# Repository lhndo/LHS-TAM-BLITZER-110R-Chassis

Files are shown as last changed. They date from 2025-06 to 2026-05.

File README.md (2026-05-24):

# LHS TAM BLITZER 1/10 R Chassis
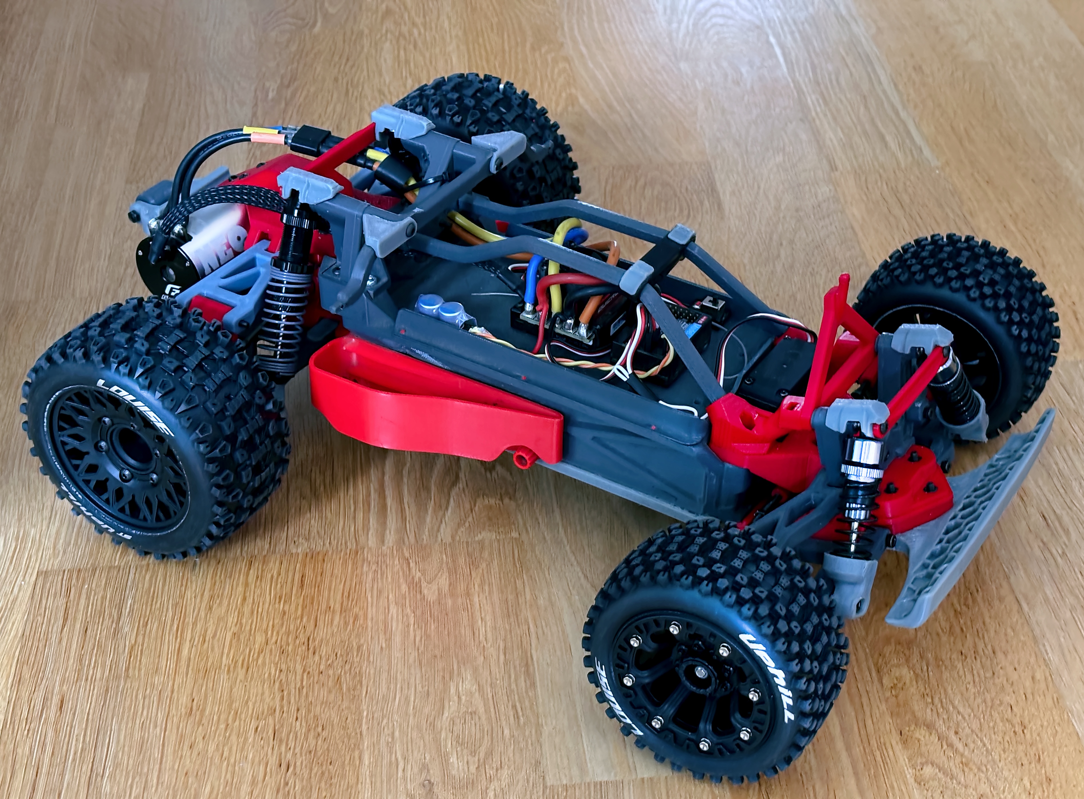
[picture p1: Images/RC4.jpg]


## Video

https://youtu.be/My_7cAeliWg

## Description

This is a FDM redesign exercise based on the 1/10 scale Tamiya Blitzer R/C chassis released in 1992 with the Tamiya Stadium Blitzer car, and later with the Tamiya Blitzer Beetle (my original kit).  

The project started with the intention of stiffening some of the original parts and having a source of spares which I could print, but ended up with a complete redesign that took a month an a half.  
I have tried to match the mounting points, so most of the parts are interchangeable with the original chassis, noting that my references were my trusty calipers and my Tamiya kit.  

The provided body posts are compatible with the Tamiya Blitzer Beetle Hard Shell Body  

### Specs

Motor: G-Force Neo Fast 13.5T Sensored Brushless Motor (2700KV) on a 13T pinion (10:1 final ratio)  
ESC: QUICRUN 10BL120 SENSORED G2  
Battery: Voltz 4600mAh 7.2V NiMh  
Weight: 2250g (4600mAh NiMh battery included)

# CAD
[Online CAD Viewer](http://tiny.cc/lhs-rc1)

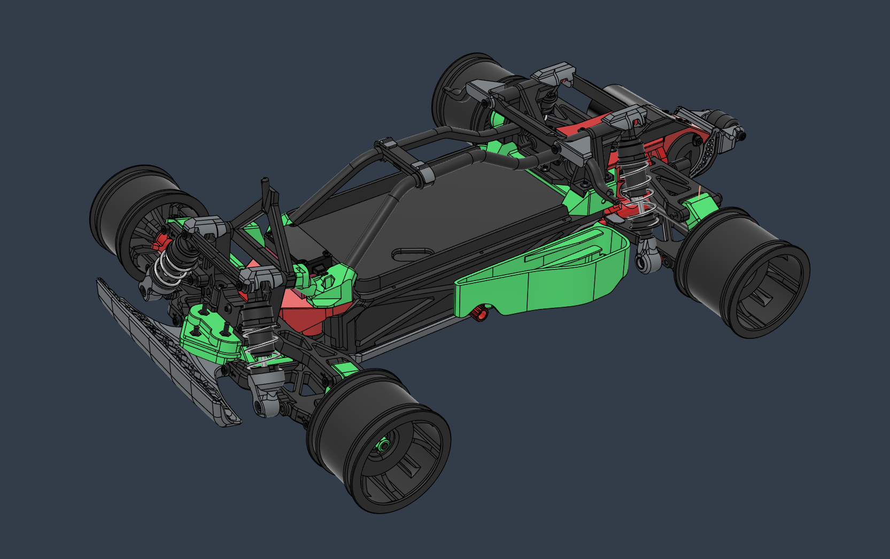
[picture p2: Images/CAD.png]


# Print

- The provided 3mf project files are set up for Orca Slicer and have extensive per-part settings for best print/performance

PLA+
_(Initial prototypes were printed in PCTG/PETG, but PLA+ with high toughness fared much better long term)_

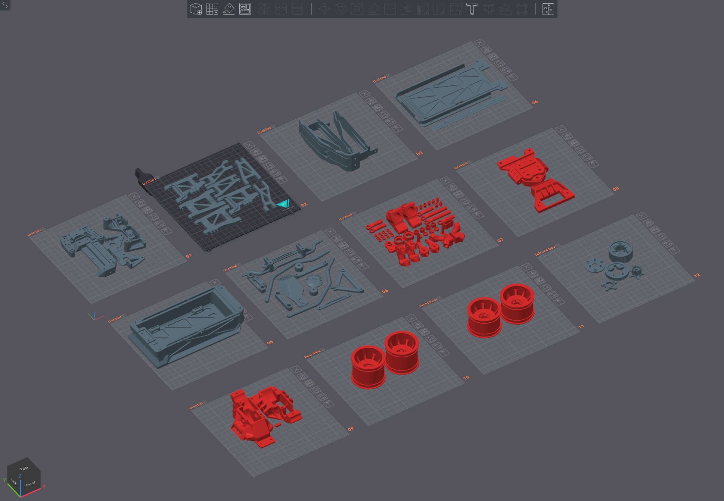
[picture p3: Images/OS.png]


TPU (95/98A)

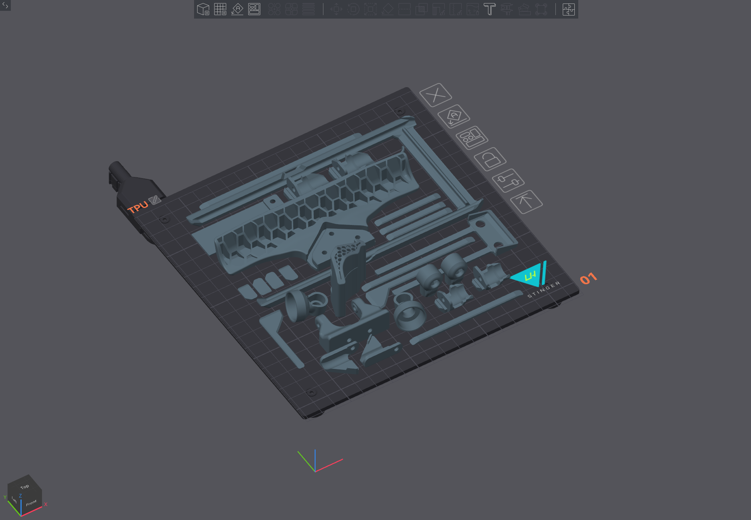
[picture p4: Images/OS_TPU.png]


# BOM

[BOM](https://docs.google.com/spreadsheets/d/1pdifgY0qCpqBBOGrd_-9JSDsqHa0moP6McLiiB6KZIc/edit?usp=sharing)

# Assembly

- Reference [Online CAD Viewer](http://tiny.cc/lhs-rc1)
- Hardware Reference Guide :

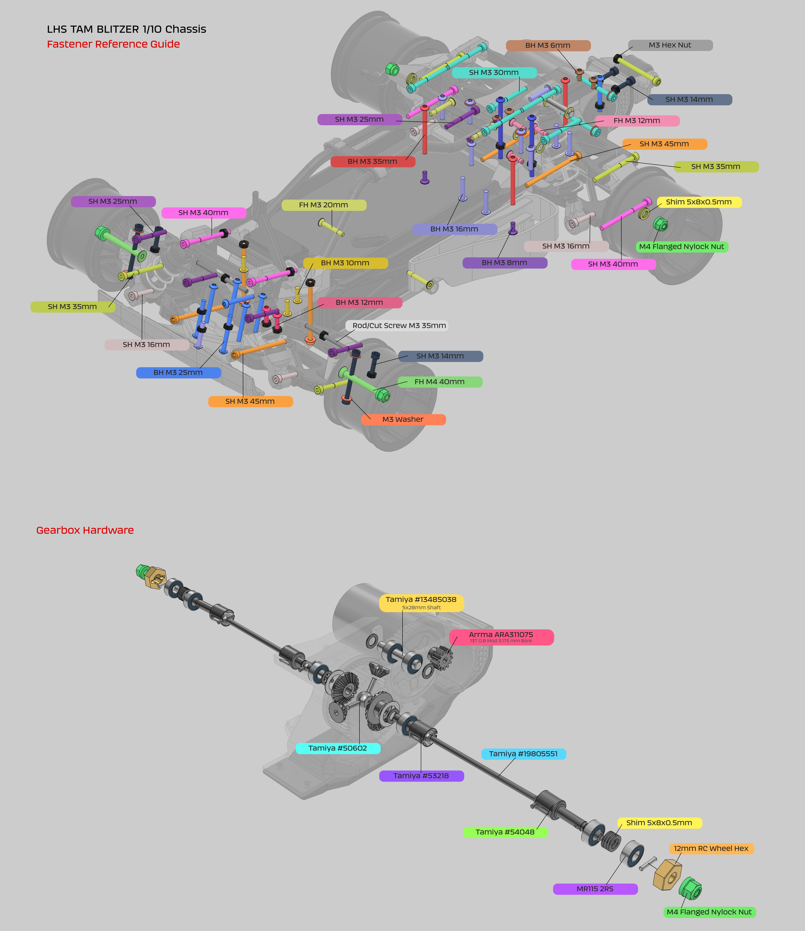
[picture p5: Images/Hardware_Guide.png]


Notes:

- Break away sacrificial bridges and clean up support areas
- The rear suspension post is composed by two parts that need to be glued together. 
  - Use filament dowels for alignment.
  - Do the same for the attachments on the main body/battery box. 
- Use an M3 tap for parts that screw directly into the plastic. These are designed with 2.6mm diameter holes that HAVE to be tapped.
- Don't over torque the screws
- Expect parts to be stiffer in the beginning and loosen up after a break-in period 
- Inject Super Lube into the holes that receive screws as axles (arms, hubs, etc). 
- Add a generous amount of Super Lube to the spur gears, differential (inside and out), and pinion gear.  
- Glue the TPU parts with Loctite Extreme Glue, Shoe Glue, E6000 etc.
- Don't overtighten the M4 lock nuts on the front wheels. Just enough so they spin freely.
- Lock the wheelie bar nut with CA glue
- Lock the middle nut on the steering faux turnbuckle screws with CA glue
- For best performance the tires will need to be set with foams and glued to the rim 
- Enjoy!

<br>

# Media





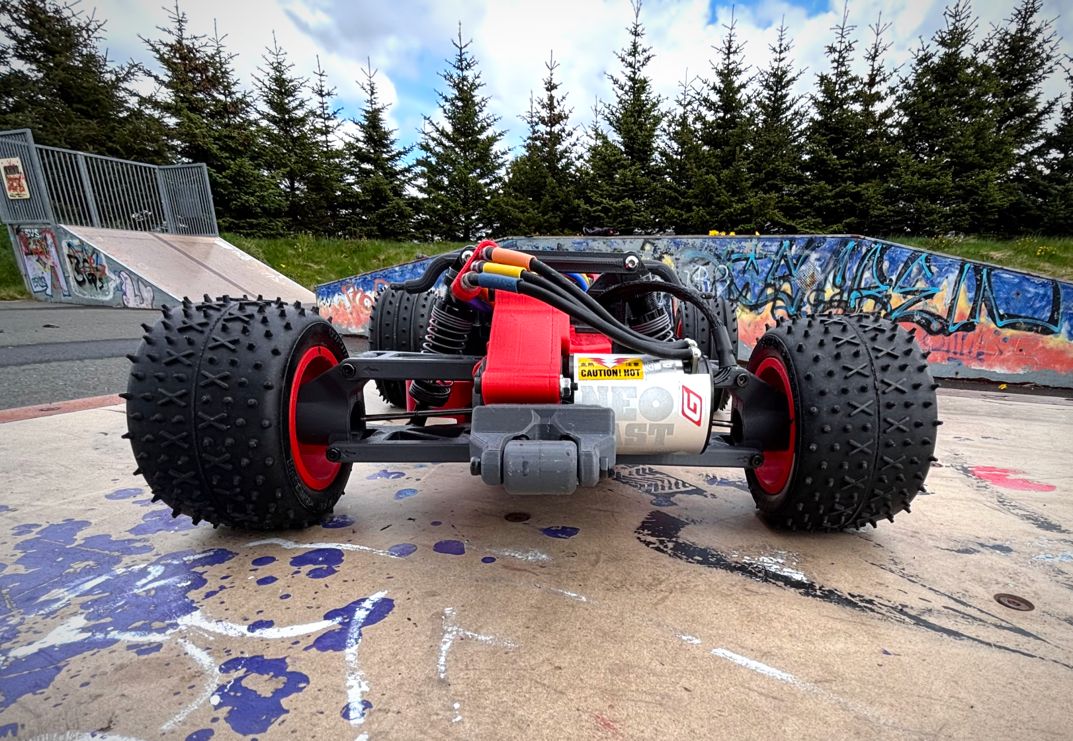
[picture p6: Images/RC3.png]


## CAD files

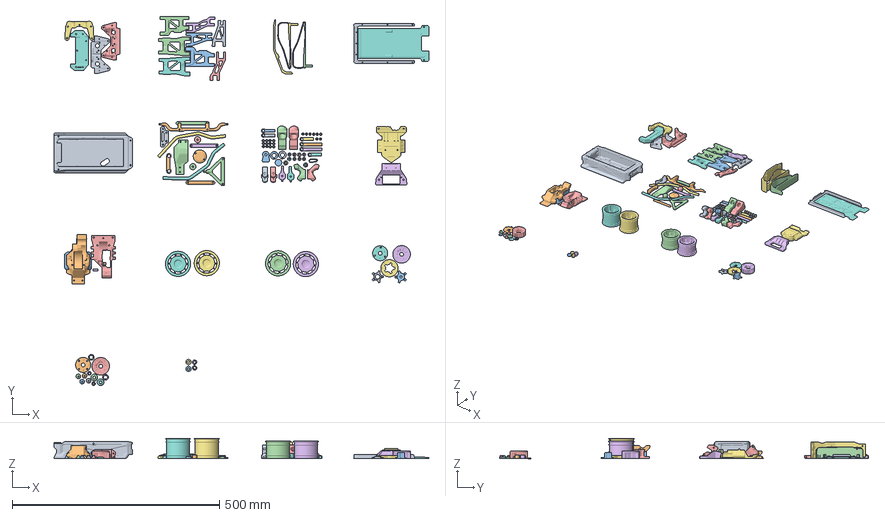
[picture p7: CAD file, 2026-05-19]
LHS-BLITZER-PTCG-PLA.3mf
903.8 x 890.1 x 49.0 mm
Rear Pillar Face.stl
Ball Connector 5.8 (2).stl x 8
ba.stl
Rear Lower Arm.stl x 2
Front Upper Arm.stl x 2
Front Shock Tower.stl
Rear Upper Arm.stl x 2
Front Tower Brace.stl
Front Lower Arm.stl x 2
Rear Tower Brace.stl
(Unsaved)
Front Upper Base.stl
Front Lower Base.stl
Rear Tower Base.stl
Tub Top.stl
Body Post Sides.stl
avv.stl
c.stl_1
c.stl_2
Dummy Front Post.stl
Rear Skidplate.stl
Tub Lid.stl
Tub.stl
Motor Cap.stl
Side Flex.stl x 2
3.stl x 4
dasc.stl x 4
sac.stl
Front Wheel.stl x 2
Roll Left.stl x 2
Roll Rear Mount.stl
Roll Brace (1) (1).stl
cc.stl x 2
Front Hub.stl x 2
Upright (2).stl x 2
M4 Sleeve.stl x 2
Gearbox Bottom.stl
Gearbox Support.stl
Gearbox Cap.stl
Gearbox Top.stl
Body41.stl
Spacer (2).stl x 12
Front Support Joint.stl x 2
Rod End 5.8mm D - long.stl x 2
Rod End 5.8mm - short.stl x 4
Body Front Post.stl
51t diff (1) (1) (1) (1).stl
Metal Diff 51T 0.8M 32P.stl
50t (2).stl
Diff Complete - Metal
50t (1).stl
51t diff (1) (3) (2) (1) (1).stl
Body2.stl
Body6.stl x 2
Body58.stl x 2
Washer (2).stl x 2
Body19.stl x 4
Rear Wheel.stl x 2
Rear Wheel Support.stl x 2
Louise 2.2 adapter outer.stl x 2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

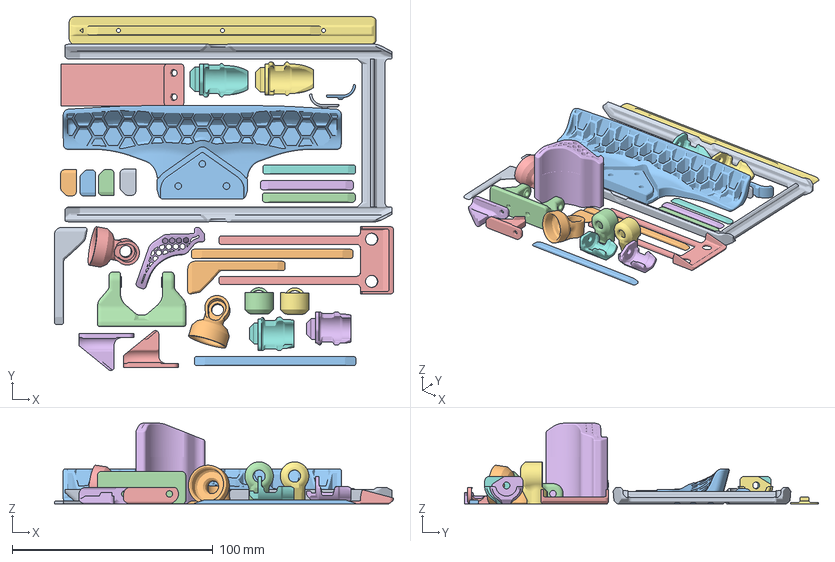
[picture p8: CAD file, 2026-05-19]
LHS-BLITZER-TPU.3mf
168.9 x 176.2 x 40.1 mm
TPU Bottom Cover.stl
Body921.stl x 2
TPU Front Bumper.stl
vdd.stl x 2
TPU Rear Skid.stl
(Unsaved)
d1.stl
ac.stl x 2
TPU Wheely Bar.stl
TPU Gearbox Insert.stl
TPU Gearbox Damper.stl
TPU Shock Rear Boot.stl x 2
TPU Top Rear Shot Cover.stl x 2
ds.stl x 2
TPU Shock Front Boot.stl x 2
TPU Top Front Shot Cover.stl x 2
TPU Rear Arm Bumper Stop.stl x 4
TPU Side Body Arm.stl x 2

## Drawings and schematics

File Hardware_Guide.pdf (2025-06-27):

## LHS TAM BLITZER 1/10 Chassis

## Fastener Reference Guide

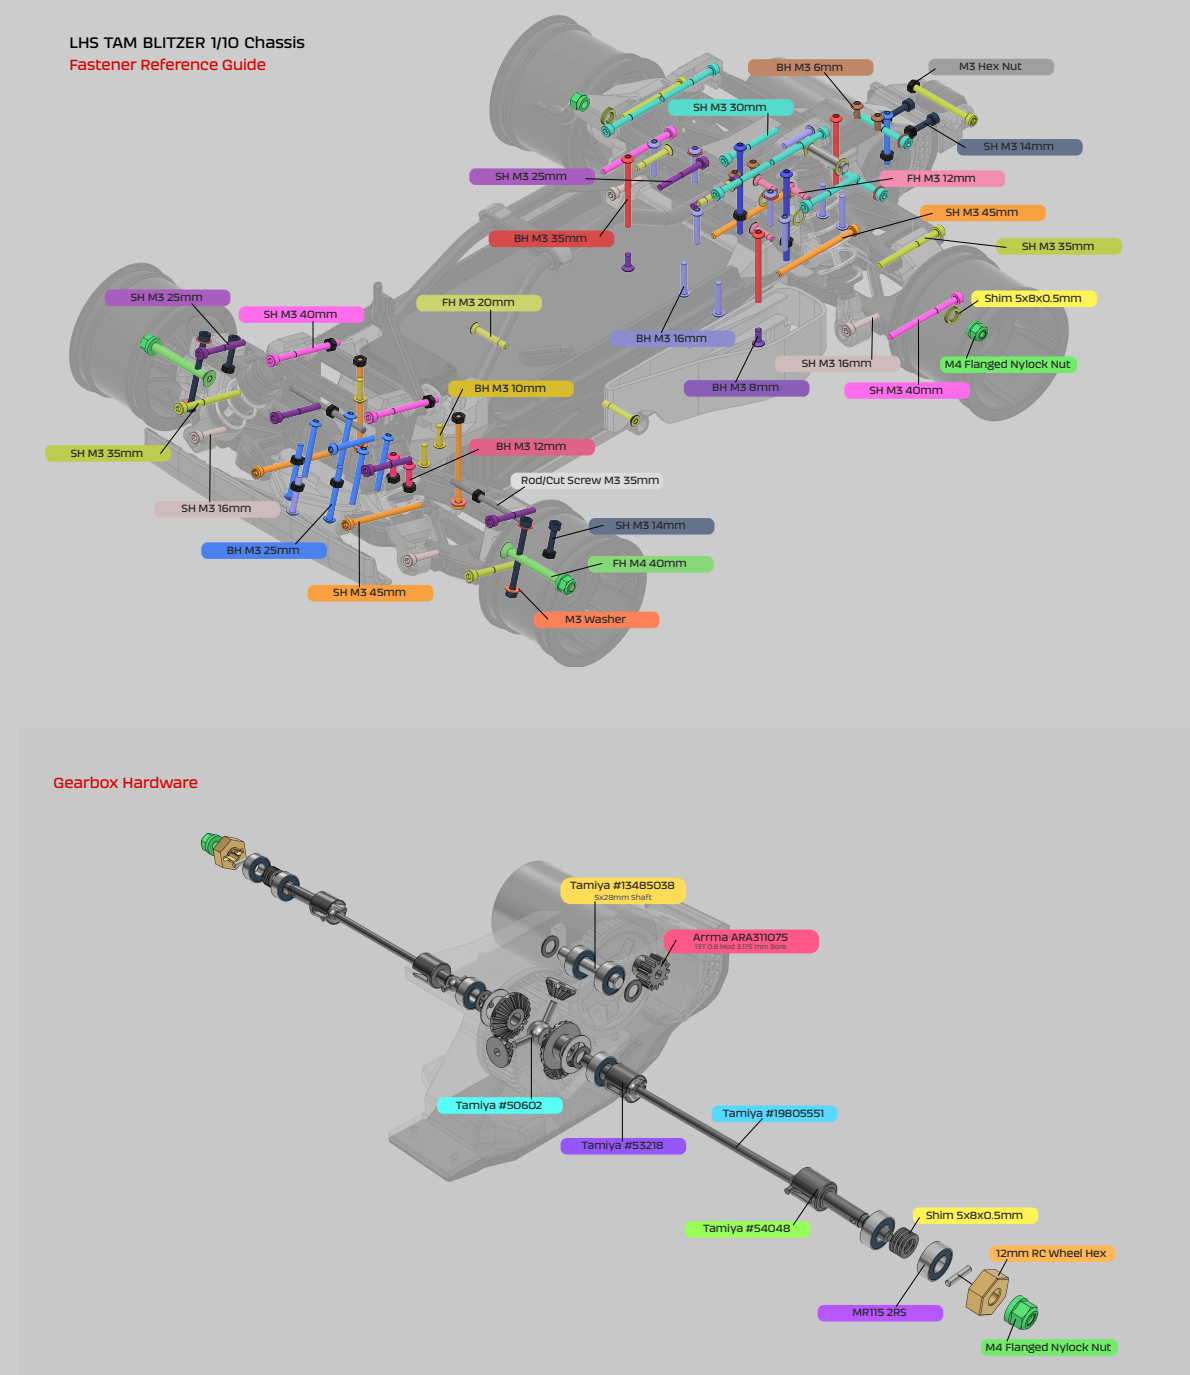
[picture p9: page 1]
Shim 5x8x0.5mm; M3 Washer; M3 Hex Nut; Gearbox Hardware; Tamiya #53218; Tamiya #13485038; 5x28mm Shaft; Tamiya #50602; Tamiya #19805551; Tamiya #54048

M4 Flanged Nylock Nut

Rod/Cut Screw M3 35mm

Arrma ARA311075
13T 0.8 Mod 3.175 mm Bore

12mm RC Wheel Hex

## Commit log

2025-06-25 update BOM
2026-05-19 updating rear diff housing cover, rear suspension post clearance, and undertray mid tpu trim
    [LHS-BLITZER-PTCG-PLA.3mf, LHS-BLITZER-TPU.3mf]
2026-05-19 fixing rear wheel rim support alignment
    [LHS-BLITZER-PTCG-PLA.3mf]
2026-05-24 change filament description
